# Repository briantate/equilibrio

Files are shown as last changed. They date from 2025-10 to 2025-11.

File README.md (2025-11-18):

# equilibrio
A ball balancing project



# Goals:
This is a learning project focused on several learning goals:
* State Space control theory
    * I will start with a simple PID controller, but move to state space control
* Zephyr OS
    * Investigate the west build system 
    * Create a custom board within Zephyr
    * 
* Cloud Connectivity
    * send ball position and other meta data to the cloud
    * Change the balls balancing location from the cloud
    * AWS IoT for the first iteration

# Future goals:
In the future, the following technologies may be added for learning:
* BLE
* Display/graphics
* Capacitive Touch may be investigated as a sensor for ball position

# Block diagram:
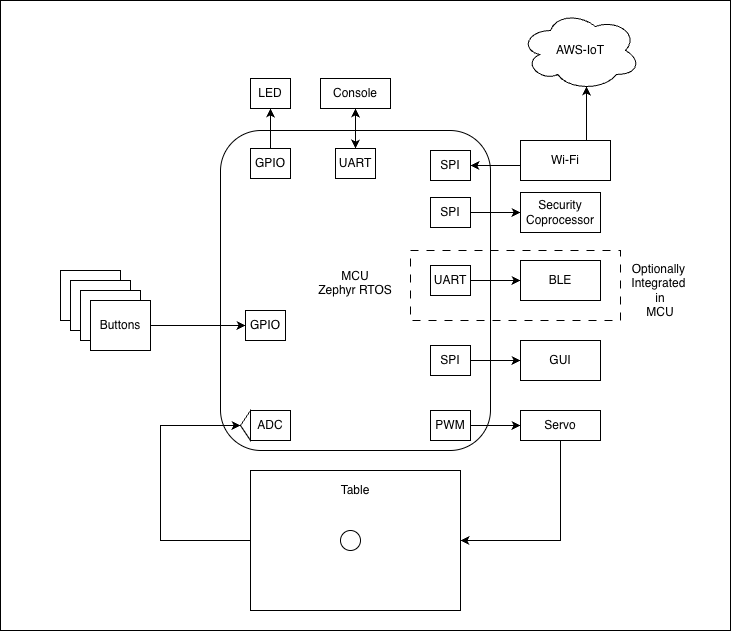
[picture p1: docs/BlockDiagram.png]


# Firmware Architecture:

# Hardware needed:
* Electronics:
    * Adafruit Metro M4 board (later to be a custom board)
    * Custom shield with headers for servo motors, touchscreen sensor, and UART header for console I/O
    * CMSIS-DAP programmer - I'm using Atmel-ICE
    * 2 MG995 180 degree metal gear servo motors
    * 2 Aluminum 25T Servo Horn Steering Arms
    * 2 RC Aluminum Linkages for Servo
    * 1 VSDISPLAY 8.4" 4 wire resistive touchscreen
* Custom balance table hardware
    * 3d-printed table hardware
    * Wooden base board to mount the table hardware

# Zephyr commands needed:
* Install the zephyr ecosystem for your OS following https://docs.zephyrproject.org/latest/develop/getting_started/index.html
* Build: need to be in the embedded_src directory
    > west build -b metro_m4 -p always -- -DBOARD_ROOT=.
    - the -DBOARD_ROOT=. tells west to look for the custom board I created in the current directory (which has the boards subdirectory)
* Flash:
    > west flash

# Notes about design choices:
* Servo:
    * I started with DS-S006L servo’s with plastic gears and plastic steering arms. These seem to work fine, but there is a lot of play in the coupling. Also, the steering arms are not very durable and split with the screws provided
    * I changed out MG995 servo’s with metal gears and steering arms. Hopefully this will reduce some of the play

* Sensor:
    * I'm using a VSDISPLAY 8.4" (172mm x 129.5mm touch area) 4-wire resistive Touch Panel I found on Amazon. I’m looking for larger (and square shaped) panels, but they get expensive quickly with increasing size
        * How 
    * When using an non-square panel, the sensor gains are different in the x and y directions. This is because the voltage drop is across a different distance in each direction, but the ADC range is the same. Ex:
        * 12b ADC = 4096 counts
        * x → 164mm/4096counts = 0.04004mm/count
        * y → 105mm/4096counts = 0x02563mm/count
    * MCU Pin voltage driving the panel lower than 3.3V:
        * The panel resistance is in the range of 300-700 ohms depending on the direction. Typical code examples for Arduino and other platforms drive this sensor with GPIO pins. This is a too much current draw for a typical GPIO pin, so the pin output voltage will drop. You can typically increase the drive strength of a GPIO, but make sure it is enough drive the load or you will measure lower voltages than expected. Ex:
            * typical default drive strength of a MCU GPIO is about 2mA
                * Max load → r=v/i = 1,650 ohms
                * at 300 ohms and 3.3V, → i=v/r = 11mA !!!
                * output pin voltage will droop to where it can actually drive this load
                * v = ir = 0.6V
    * Seeing a strange offset in the sensor reading when no touch is present:
        * The panel some capacitance between the two layers of ITO, and the ADC has some sample capacitance (2-3pF). When you switch on voltage across one layer while the other layer is floating (high impedance into your ADC) and no touch is present, this sensed line voltage will jump to about ½ of the driven voltage and then very slowly decay back to 0. This is because, with no touch, there is very high (almost infinite) resistance between in the sensed line because it’s floating. This causes a large RC time constant. If you sample the line before this decays, you will read the floating voltage instead of the actual voltages
        * My quick solution was to add some pull-down resistance to the sampled lines of the touch panel. I used 5k because I had these in my stock. This does cause a small voltage drop in the reading (but can be accounted for) and significantly speeds up the decay of this voltage, effectively removing the offset from the reading

* Balance table:
    * the play in the servo coupling was accentuated by my initial table design which had the fixed table mount in the middle of the sensing table. This puts the servo load in both tension and compression depending on the position of the ball. If the ball is between the fixed table mount and the servo, the linkage is in compression. If the ball is past the fixed table mount from the servo, the linkage is in tension. When it switches between tension and compression, the play in the linkage causes some error in the actuation of the table. I changed my design to put a fixed table mount on one side of the table, and then put the servo linkage connections at the two opposite corners of the table. This causes the linkage to always be in compression, removing the "transition play"

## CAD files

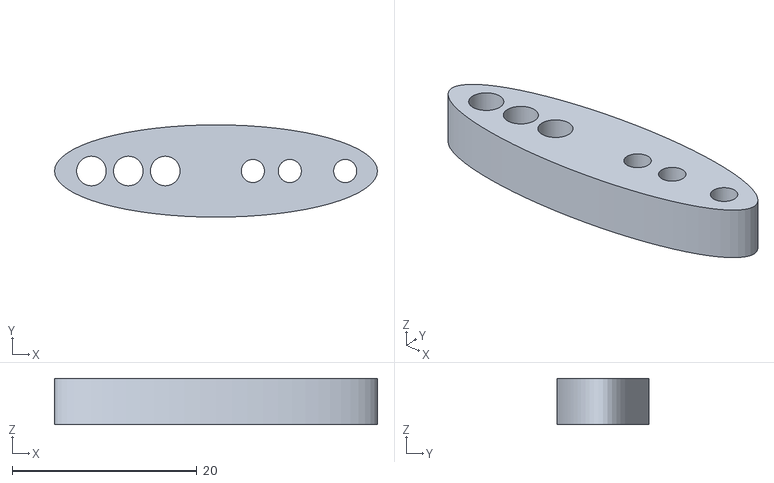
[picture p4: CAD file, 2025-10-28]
3d/Tie Rod Adapter.stl
35.0 x 10.0 x 5.00

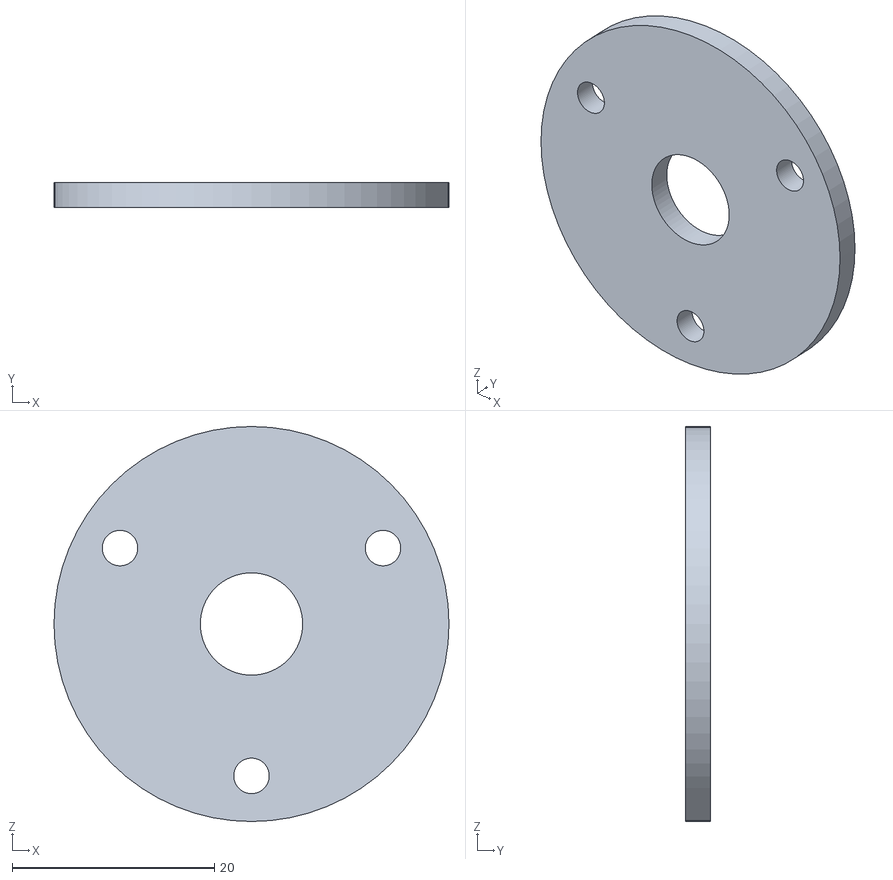
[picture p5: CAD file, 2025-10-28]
3d/Potentiometer Adapter.stl
39.0 x 2.50 x 39.0

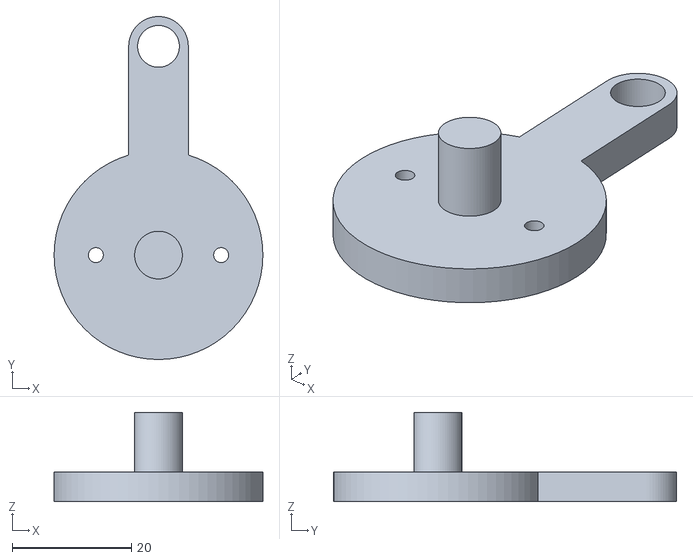
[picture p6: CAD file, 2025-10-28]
3d/ServoCoupler.stl
35.0 x 57.5 x 15.0

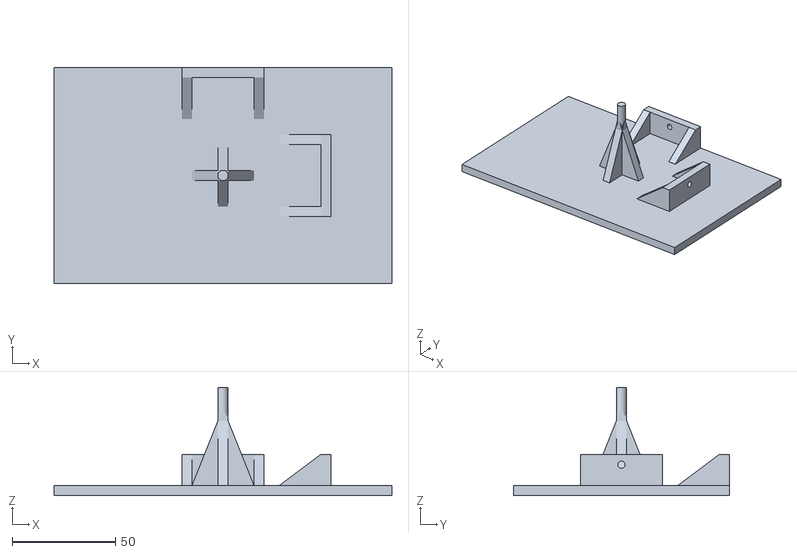
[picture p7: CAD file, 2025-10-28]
3d/balance_board.stl
164.0 x 105.0 x 52.5

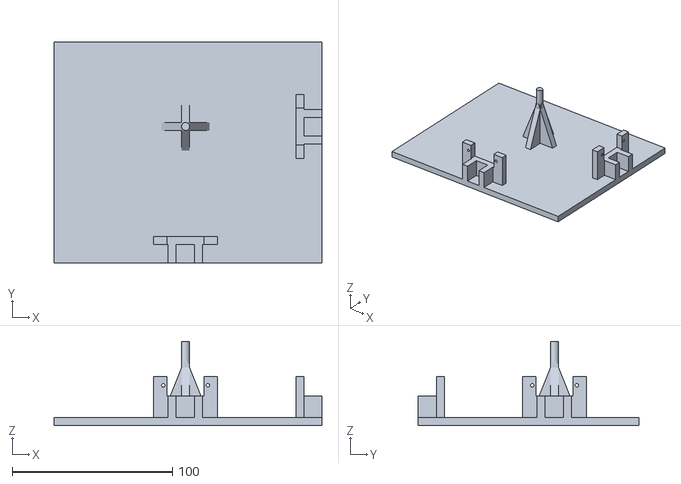
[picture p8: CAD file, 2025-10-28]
3d/balance_base.stl
167.0 x 137.5 x 52.5

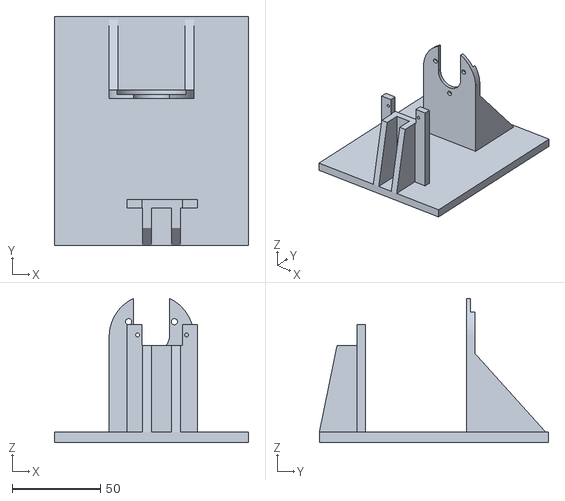
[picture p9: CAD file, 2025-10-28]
3d/ServoCharBench.stl
110.0 x 130.0 x 81.7

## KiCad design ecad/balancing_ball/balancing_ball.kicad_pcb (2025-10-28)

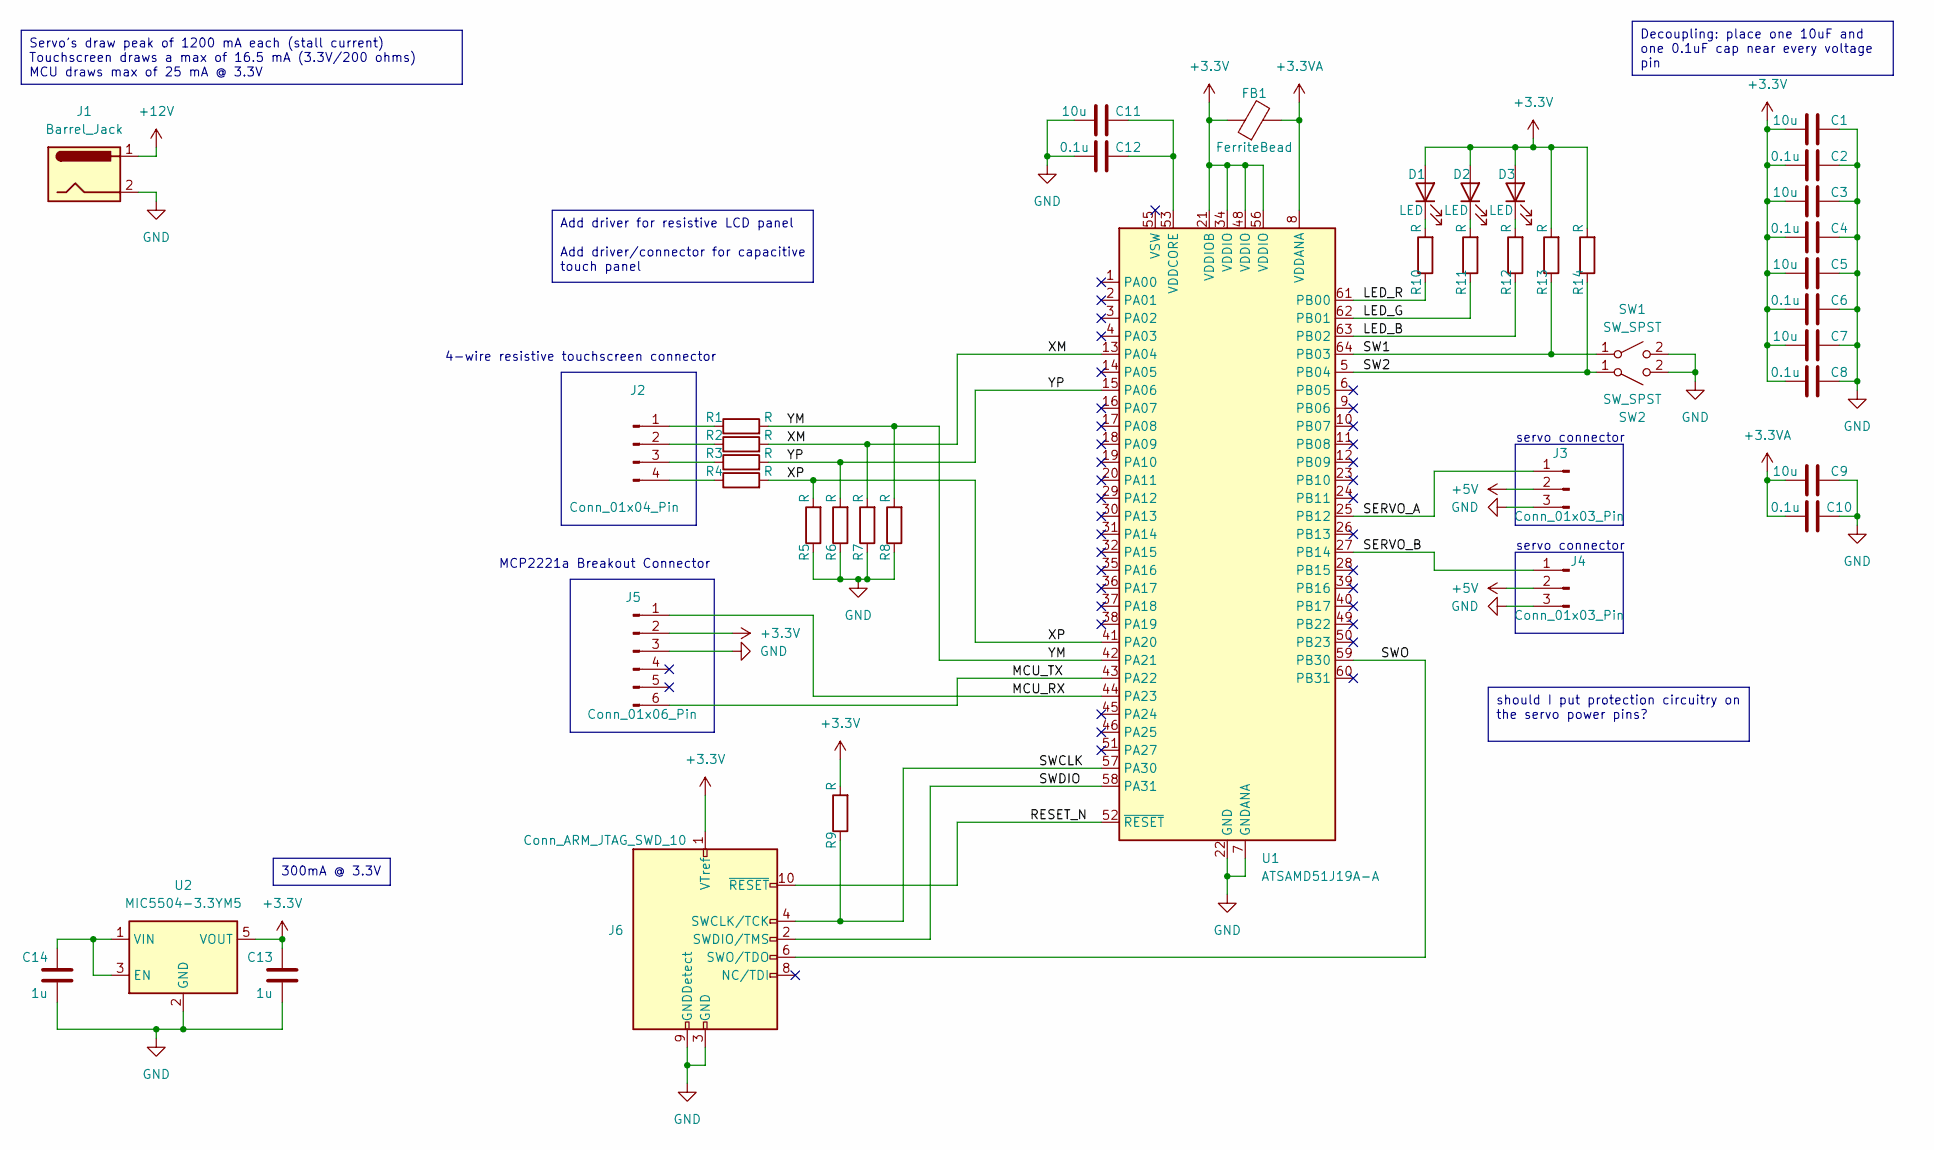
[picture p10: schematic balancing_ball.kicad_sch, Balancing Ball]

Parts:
C1, C3, C5, C7, C9, C11: 10u; R_0603_1608Metric
C2, C4, C6, C8, C10, C12: 0.1u; R_0603_1608Metric
C13, C14: 1u; R_0603_1608Metric
D1, D2, D3: LED; D_0603_1608Metric
FB1: FerriteBead; L_0603_1608Metric
J1: Barrel_Jack
J2: Conn_01x04_Pin; PinHeader_1x04_P2.54mm_Horizontal
J3, J4: Conn_01x03_Pin; PinHeader_1x03_P2.54mm_Horizontal
J5: Conn_01x06_Pin; PinHeader_1x06_P2.54mm_Horizontal
J6: Conn_ARM_JTAG_SWD_10; PinSocket_2x05_P1.27mm_Vertical
R1, R2, R3, R4, R5, R6, R7, R8, R9, R10, R11, R12, R13, R14: R; R_0603_1608Metric
SW1, SW2: SW_SPST; SW_Push_1P1T_NO_Vertical_Wuerth_434133025816
U1: ATSAMD51J19A-A; TQFP-64_10x10mm_P0.5mm
U2: MIC5504-3.3YM5; SOT-23-5

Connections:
+3.3V: C1.1, C2.1, C3.1, C4.1, C5.1, C6.1, C7.1, C8.1, C13.1, D1.2 (A), D2.2 (A), D3.2 (A), FB1.1, J5.2, J6.1 (VTref), R9.2, R13.2, R14.2, U1.21 (VDDIOB), U1.34 (VDDIO), U1.48 (VDDIO), U1.56 (VDDIO), U2.5 (VOUT)
+3.3VA: C9.1, C10.1, FB1.2, U1.8 (VDDANA)
+5V: J3.2, J4.2
/LED_B: R12.1, U1.63 (PB02)
/LED_G: R11.1, U1.62 (PB01)
/LED_R: R10.1, U1.61 (PB00)
/MCU_RX: J5.1, U1.44 (PA23)
/MCU_TX: J5.6, U1.43 (PA22)
/RESET_N: J6.10 (~RESET), U1.52 (~RESET)
/SERVO_A: J3.1, U1.25 (PB12)
/SERVO_B: J4.1, U1.27 (PB14)
/SW1: R13.1, SW1.1 (A), U1.64 (PB03)
/SW2: R14.1, SW2.1 (A), U1.5 (PB04)
/SWCLK: J6.4 (SWCLK/TCK), R9.1, U1.57 (PA30)
/SWDIO: J6.2 (SWDIO/TMS), U1.58 (PA31)
/SWO: J6.6 (SWO/TDO), U1.59 (PB30)
/XM: R2.2, R7.2, U1.13 (PA04)
/XP: R4.2, R5.2, U1.41 (PA20)
/YM: R1.2, R8.2, U1.42 (PA21)
/YP: R3.2, R6.2, U1.15 (PA06)
GND: C1.2, C2.2, C3.2, C4.2, C5.2, C6.2, C7.2, C8.2, C9.2, C10.2, C11.1, C12.1, C13.2, C14.2, J1.2, J3.3, J4.3, J5.3, J6.3 (GND), J6.5 (GND), J6.9 (GNDDetect), R5.1, R6.1, R7.1, R8.1, SW1.2 (B), SW2.2 (B), U1.7 (GNDANA), U1.22 (GND), U1.33 (GND), U1.47 (GND), U1.54 (GND), U2.2 (GND)
unnamed: D1.1 (K), R10.2
unnamed: D2.1 (K), R11.2
unnamed: D3.1 (K), R12.2
unnamed: J2.1, R1.1
unnamed: J2.2, R2.1
unnamed: J2.3, R3.1
unnamed: J2.4, R4.1
unnamed: C11.2, C12.2, U1.53 (VDDCORE)
unnamed: C14.1, U2.1 (VIN), U2.3 (EN)

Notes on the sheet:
should I put protection circuitry on the servo power pins?
300mA @ 3.3V
Add driver for resistive LCD panel Add driver/connector for capacitive touch panel
Servo's draw peak of 1200 mA each (stall current) Touchscreen draws a max of 16.5 mA (3.3V/200 ohms) MCU draws max of 25 mA @ 3.3V
Decoupling: place one 10uF and one 0.1uF cap near every voltage pin
MCP2221a Breakout Connector
servo connector
4-wire resistive touchscreen connector

Board: 2 copper layers, 41 parts (0 on the bottom side), 30 nets, no tracks yet.

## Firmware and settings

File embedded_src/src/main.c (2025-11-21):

#include <zephyr/kernel.h>
#include <zephyr/device.h>
#include <zephyr/sys/printk.h>

#include <zephyr/drivers/pwm.h>
#include "pid.h"
#include "resistive_touch_sensor.h"

#define STEP PWM_USEC(100)
#define SAMPLE_RATE (20) //ms

//Servos
#define SERVO_MID_US (PWM_USEC(1439))
#define SERVO_STEP (SERVO_MID_US - PWM_USEC(10))

uint32_t pid_x_output = SERVO_MID_US;
uint32_t pid_y_output = SERVO_MID_US;

static const struct pwm_dt_spec servo_left = PWM_DT_SPEC_GET(DT_NODELABEL(servo_left));
static const struct pwm_dt_spec servo_right = PWM_DT_SPEC_GET(DT_NODELABEL(servo_right));
//Note - min and max are the same for both servos
static const uint32_t min_pulse = DT_PROP(DT_NODELABEL(servo_left), min_pulse);
static const uint32_t max_pulse = DT_PROP(DT_NODELABEL(servo_left), max_pulse);

uint16_t sensorX_val = 0;
uint16_t sensorY_val = 0;
bool last_ball_state = true;

// PID
pid_t pid_x = {
	.kp = 4,
	.ki = 0.2,
	.kd = 3100,
	.error_last = 0,
	.PID_i = 0,
	.sampling_period = SAMPLE_RATE
};

pid_t pid_y = {
	.kp = 4,
	.ki = 0.2,
	.kd = 3100,
	.error_last = 0,
	.PID_i = 0,
	.sampling_period = SAMPLE_RATE
};

// private prototypes:
static bool isBallDetected(uint16_t x, uint16_t y);
static long map(long x, long in_min, long in_max, long out_min, long out_max);

//public functions

int main(void)
{
	printk("Amazing Balancing Ball!!!\r\n");

	int err;

	// check if gpio are ready //ToDo: is this needed?
	printk("check if gpio are ready\r\n");
	if (!gpio_is_ready_dt(&x_m_pin)) {
		printk("x_m_pin port is not ready.\n");
		return 0;
	}
	if (!gpio_is_ready_dt(&x_p_pin)) {
		printk("x_p_pin port is not ready.\n");
		return 0;
	}
	if (!gpio_is_ready_dt(&y_m_pin)) {
		printk("y_m_pin port is not ready.\n");
		return 0;
	}
	if (!gpio_is_ready_dt(&y_p_pin)) {
		printk("y_p_pin port is not ready.\n");
		return 0;
	}

    //configure pins
	printk("configure gpio\r\n");
	err = gpio_pin_configure_dt(&x_m_pin, GPIO_OUTPUT_INACTIVE);
	if (err != 0) {
		printk("Configuring GPIO pin failed: %d\n", err);
		return 0;
	}
	err = gpio_pin_configure_dt(&x_p_pin, GPIO_OUTPUT_INACTIVE);
	if (err != 0) {
		printk("Configuring GPIO pin failed: %d\n", err);
		return 0;
	}
	err = gpio_pin_configure_dt(&y_m_pin, GPIO_OUTPUT_INACTIVE);
	if (err != 0) {
		printk("Configuring GPIO pin failed: %d\n", err);
		return 0;
	}
	err = gpio_pin_configure_dt(&y_p_pin, GPIO_OUTPUT_INACTIVE);
	if (err != 0) {
		printk("Configuring GPIO pin failed: %d\n", err);
		return 0;
	}

	//configure adc
	printk("configure adc\r\n");
	if(!device_is_ready(touch_sensor_adc)){
		printk("Touch Sensor is not ready\r\n");
		return 0;
	}

	err = adc_channel_setup(touch_sensor_adc, &touch_sensor_adc_x);
	if(err<0){
		printk("Could not set up touch sensor x\r\n");
		return 0;
	}

	err = adc_channel_setup(touch_sensor_adc, &touch_sensor_adc_y);
	if(err<0){
		printk("Could not set up touch sensor y\r\n");
		return 0;
	}


    uint32_t pulse_width_left = SERVO_MID_US;
    uint32_t pulse_width_right = SERVO_MID_US;

	//
	printk("check if pwms are ready\r\n");
	if (!pwm_is_ready_dt(&servo_left)) {
		printk("Error: PWM device %s is not ready\n",
		       servo_left.dev->name);
		return 0;
	}
	if (!pwm_is_ready_dt(&servo_right)) {
		printk("Error: PWM device %s is not ready\n",
		       servo_right.dev->name);
		return 0;
	}

	//level the table
	pwm_set_pulse_dt(&servo_left, pulse_width_left);
	pwm_set_pulse_dt(&servo_right, pulse_width_right);

    while (1) {

		sensorX_val = touch_sensor_read_x();
		sensorY_val = touch_sensor_read_y();
		// sensorX_val = touch_sensor_read(&sensor_x);
		// sensorY_val = touch_sensor_read(&sensor_y);
		printk("x: %u ", sensorX_val);
		printk("y: %u\r\n", sensorY_val);
		
		bool is_ball_detected = isBallDetected(sensorX_val,sensorY_val);
		if(!is_ball_detected){
			if(last_ball_state)
				printk("no ball detected\r\n");

			pid_x_output = SERVO_MID_US;
			pid_y_output = SERVO_MID_US;
			pid_clear_values(&pid_x);
			pid_clear_values(&pid_y);
		}
		else{ 
			if(!last_ball_state)
				printk("ball detected\r\n");

			pid_x_output = pid_control(&pid_x, TOUCHSCREEN_CENTER, sensorX_val);
			pulse_width_left = map(pid_x_output, -16000, 16000, min_pulse, max_pulse);
			pid_y_output = pid_control(&pid_y, sensorY_val, TOUCHSCREEN_CENTER);
			pulse_width_right = map(pid_y_output, -16000, 16000, min_pulse, max_pulse);
		}
		last_ball_state = is_ball_detected;

        err = pwm_set_pulse_dt(&servo_left, pulse_width_left);
        if (err < 0) {
			printk("Error %d: failed to set pulse width left\n", err);
			return 0;
		}

        err = pwm_set_pulse_dt(&servo_right, pulse_width_right);
		if (err < 0) {
			printk("Error %d: failed to set pulse width right\n", err);
			return 0;
		}

        k_sleep(K_MSEC(SAMPLE_RATE));
    }
}

// private functions:

static bool isBallDetected(uint16_t x, uint16_t y)
{
    return((x > 300) && (y > 300));
}

// helper function to map a value from one range to another
static long map(long x, long in_min, long in_max, long out_min, long out_max) {
  return (x - in_min) * (out_max - out_min) / (in_max - in_min) + out_min;
}

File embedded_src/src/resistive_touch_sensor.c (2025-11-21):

#include "resistive_touch_sensor.h"
#include <zephyr/drivers/adc.h>
#include <zephyr/drivers/gpio.h>

// uint16_t touch_sensor_read(touch_sensor_t *sensor){
// 	uint16_t value;
// 	//Set x pins to outputs
// 	//Set y pins to inputs
// 	//drive xm low
// 	//drive xp high
// 	sensor->high_z_pin_1();
// 	sensor->high_z_pin_2();
// 	sensor->drive_high_pin();
// 	sensor->drive_low_pin();

// 	//wait for settling period
// 	sensor->wait_to_settle();

// 	//read ADC
// 	value = sensor->adc_read();

// 	// set xp low
// 	// restore all pins to high z
// 	return value;
// }

//ADC's
#define TOUCH_SENSOR_X DT_ALIAS(adc_touch_sensor_x)
#define TOUCH_SENSOR_Y DT_ALIAS(adc_touch_sensor_y)
static const struct device *touch_sensor_adc = DEVICE_DT_GET(DT_ALIAS(adc_touch_sensor));
static const struct adc_channel_cfg touch_sensor_adc_x = ADC_CHANNEL_CFG_DT(TOUCH_SENSOR_X);
static const struct adc_channel_cfg touch_sensor_adc_y = ADC_CHANNEL_CFG_DT(TOUCH_SENSOR_Y);

uint16_t buf_x;
uint16_t val_mv_x;
uint32_t vref_mv_x = DT_PROP(TOUCH_SENSOR_X, zephyr_vref_mv);

uint16_t buf_y;
uint16_t val_mv_y;
uint32_t vref_mv_y = DT_PROP(TOUCH_SENSOR_Y, zephyr_vref_mv);

struct adc_sequence seq_x = {
	.channels = BIT(touch_sensor_adc_x.channel_id),
	.buffer = &buf_x,
	.buffer_size = sizeof(buf_x),
	.resolution = DT_PROP(TOUCH_SENSOR_X, zephyr_resolution)
};

struct adc_sequence seq_y = {
	.channels = BIT(touch_sensor_adc_y.channel_id),
	.buffer = &buf_y,
	.buffer_size = sizeof(buf_y),
	.resolution = DT_PROP(TOUCH_SENSOR_Y, zephyr_resolution)
};

//GPIO's 
static const struct gpio_dt_spec x_m_pin = GPIO_DT_SPEC_GET(DT_NODELABEL(x_m_pin), gpios);
static const struct gpio_dt_spec x_p_pin = GPIO_DT_SPEC_GET(DT_NODELABEL(x_p_pin), gpios);
static const struct gpio_dt_spec y_m_pin = GPIO_DT_SPEC_GET(DT_NODELABEL(y_m_pin), gpios);
static const struct gpio_dt_spec y_p_pin = GPIO_DT_SPEC_GET(DT_NODELABEL(y_p_pin), gpios);


int touch_sensor_init(void){
    int err;
    //check if gpio are ready //ToDo: is this needed?
	printk("check if gpio are ready\r\n");
	if (!gpio_is_ready_dt(&x_m_pin)) {
		printk("x_m_pin port is not ready.\n");
		return 0;
	}
	if (!gpio_is_ready_dt(&x_p_pin)) {
		printk("x_p_pin port is not ready.\n");
		return 0;
	}
	if (!gpio_is_ready_dt(&y_m_pin)) {
		printk("y_m_pin port is not ready.\n");
		return 0;
	}
	if (!gpio_is_ready_dt(&y_p_pin)) {
		printk("y_p_pin port is not ready.\n");
		return 0;
	}

    //configure pins
	printk("configure gpio\r\n");
	err = gpio_pin_configure_dt(&x_m_pin, GPIO_OUTPUT_INACTIVE);
	if (err != 0) {
		printk("Configuring GPIO pin failed: %d\n", err);
		return 0;
	}
	err = gpio_pin_configure_dt(&x_p_pin, GPIO_OUTPUT_INACTIVE);
	if (err != 0) {
		printk("Configuring GPIO pin failed: %d\n", err);
		return 0;
	}
	err = gpio_pin_configure_dt(&y_m_pin, GPIO_OUTPUT_INACTIVE);
	if (err != 0) {
		printk("Configuring GPIO pin failed: %d\n", err);
		return 0;
	}
	err = gpio_pin_configure_dt(&y_p_pin, GPIO_OUTPUT_INACTIVE);
	if (err != 0) {
		printk("Configuring GPIO pin failed: %d\n", err);
		return 0;
	}

	//configure adc
	printk("configure adc\r\n");
	if(!device_is_ready(touch_sensor_adc)){
		printk("Touch Sensor is not ready\r\n");
		return 0;
	}

	err = adc_channel_setup(touch_sensor_adc, &touch_sensor_adc_x);
	if(err<0){
		printk("Could not set up touch sensor x\r\n");
		return 0;
	}

	err = adc_channel_setup(touch_sensor_adc, &touch_sensor_adc_y);
	if(err<0){
		printk("Could not set up touch sensor y\r\n");
		return 0;
	}

    return 0;
}

uint16_t touch_sensor_read_x(void){

    int err = 0;
	err =  gpio_pin_configure_dt(&x_m_pin, GPIO_OUTPUT);
    err += gpio_pin_configure_dt(&x_p_pin, GPIO_OUTPUT);
    err += gpio_pin_configure_dt(&y_m_pin, GPIO_INPUT);
    err += gpio_pin_configure_dt(&y_p_pin, GPIO_INPUT);

	if(err != 0){
		printk("error configuring GPIO before measurement\r\n");
		return 0;
	}
    
	err = 0;
    err =  gpio_pin_set_dt(&x_p_pin, 0);
    err += gpio_pin_set_dt(&x_m_pin, 1);

	if(err != 0){
		printk("error setting GPIO before measurement\r\n");
		return 0;
	}

    k_sleep(K_MSEC(1));

	int ret = adc_read(touch_sensor_adc, &seq_x);
	if(ret<0){
		printk("Could not read touch sensor x: %d\r\n", ret);
	}
	val_mv_x = buf_x * vref_mv_x /(1 << seq_x.resolution);
	// printk("X RAW: %u, mV: %u\r\n", buf_x, val_mv_x);

	err = 0;
    err = gpio_pin_set_dt(&x_m_pin, 0);
	if(err != 0){
		printk("error setting GPIO after measurement\r\n");
		return 0;
	}

	err = 0;
    err =  gpio_pin_configure_dt(&x_m_pin, GPIO_INPUT);
    err += gpio_pin_configure_dt(&x_p_pin, GPIO_INPUT);
	if(err != 0){
		printk("error configuring GPIO after measurement\r\n");
		return 0;
	}

  return(val_mv_x);
    
}

uint16_t touch_sensor_read_y(void){

	int err = 0;
    err =  gpio_pin_configure_dt(&x_m_pin, GPIO_INPUT);
    err += gpio_pin_configure_dt(&x_p_pin, GPIO_INPUT);
    err += gpio_pin_configure_dt(&y_m_pin, GPIO_OUTPUT);
    err += gpio_pin_configure_dt(&y_p_pin, GPIO_OUTPUT);

	if(err != 0){
		printk("error configuring GPIO before measurement\r\n");
		return 0;
	}
    
	err = 0;
    err =  gpio_pin_set_dt(&y_p_pin, 0);
    err += gpio_pin_set_dt(&y_m_pin, 1);

	if(err != 0){
		printk("error setting GPIO before measurement\r\n");
		return 0;
	}

    k_sleep(K_MSEC(1));

	int ret = adc_read(touch_sensor_adc, &seq_y);
	if(ret<0){
		printk("Could not read touch sensor y: %d\r\n", ret);
	}
	val_mv_y = buf_y * vref_mv_y /(1 << seq_y.resolution);
	// printk("Y RAW: %u, mV: %u\r\n", buf_y, val_mv_y);

	err = 0;
    err = gpio_pin_set_dt(&y_m_pin, 0);

	if(err != 0){
		printk("error setting GPIO after measurement\r\n");
		return 0;
	}

	err = 0;
    err = gpio_pin_configure_dt(&y_m_pin, GPIO_INPUT);
    err += gpio_pin_configure_dt(&y_p_pin, GPIO_INPUT);
	if(err != 0){
		printk("error configuring GPIO after measurement\r\n");
		return 0;
	}


    return(val_mv_y);
}

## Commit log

2025-10-28 add base project files
    [Potentiometer Adapter.stl, ServoCharBench.stl, ServoCoupler.stl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]
2025-11-13 add servo's on pb14 and pb15
    [pwm-servo.yaml]
2025-11-13 add board files for metro_m4
2025-11-14 update servo min and max to match MG995 settings from my previous project
2025-11-17 add adc channel placeholders in the device tree - doesn't compile
    [main.c]
2025-11-18 add gpio sample code and dt settings
2025-11-18 add back in adc settings in device tree
2025-11-18 move adc and gpio into touch sensor module
2025-11-19 add pid code
2025-11-21 refactor pid code with object pattern
